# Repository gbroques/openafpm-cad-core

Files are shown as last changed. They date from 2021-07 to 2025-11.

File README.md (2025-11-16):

# OpenAFPM CAD Core

Repository containing [OpenAFPM](https://www.openafpm.net/) wind turbine CAD model, and models for tools aiding in the local construction of the wind turbine such as molds and jigs.

The wind turbine design is based on ["*A Wind Turbine Recipe Book*" by Hugh Piggott](http://scoraigwind.co.uk/pdf-metric-edition-of-recipe-book-at-scribd/).

All models are made with the open-source CAD program [FreeCAD](https://www.freecad.org/).

Various functions (yet to be described) are exposed to support other projects. See [Related Repositories](#related-repositories).

## Installing Package

From the root of this repository:

    pip install --editable .

## Installing Macros

From the root of this repository:

    ./link_macros.bash

## Related Repositories
* [openafpm_worker/MagnAFPM](https://gitlab.com/rurerg/openafpm/openafpm_worker/-/tree/master/MagnAFPM) - simulates AFPM generator and generates output for CAD model.
* [openafpm-cad-visualization](https://github.com/gbroques/openafpm-cad-visualization) - visualizes CAD models in a web browser.
* [openafpm-cad-desktop-app](https://github.com/gbroques/openafpm-cad-desktop-app) - for **testing** `openafpm-cad-core` and `openafpm-cad-visualization`.

## Prerequisites

1. Install [Micromamba](https://mamba.readthedocs.io/en/latest/installation/micromamba-installation.html).

## Setup
Execute the following commands from the root of this repository.

1. Create `openafpm-cad-core` conda environment.

       micromamba env create --file environment.yml

2. Activate `openafpm-cad-core` environment.

       micromamba activate openafpm-cad-core

3. Add the `$CONDA_PREFIX/lib` directory to `$PYTHONPATH` (this allows `FreeCAD` to be imported as a module within python).

       ./add_conda_path_to_python_path.sh

4. Deactivate and re-activate `openafpm-cad-core` environment.

       micromamba deactivate && micromamba activate openafpm-cad-core

5. Verify `freecad` executable is accessible:

       freecad --version

## Docs
Run `./make_docs.sh` from `docs/` with `openafpm-cad-core` conda environment activated.

## How to Upgrade FreeCAD Version
The version of FreeCAD is defined in `environment.yml` within the root of this repository.

1. Check if there's a newer version from FreeCAD's [GitHub releases page](https://github.com/FreeCAD/FreeCAD/releases) or [Wiki](https://wiki.freecad.org/Feature_list#Release_notes).
2. Increase version for `freecad` in `environment.yml`.
3. Remove `openafpm-cad-core` conda environment created in the "Setup" section.

       micromamba remove --name openafpm-cad-core --all

4. Reperform steps in the [Setup](#setup) section to recreate `openafpm-cad-core` conda environment.
5. Regression test all functionality. (TODO: Write documentation for this)
6. Update "Supported FreeCAD Versions" section in [README.md](./README.md).

## Generating Files for openafpm-cad-visualization

1. Activate the `openafpm-cad-core` conda environment.
2. If `openafpm-cad-visualization` is cloned up a directory from this repository, then run:

       python macros/visualize.py ../openafpm-cad-visualization/public/
       python macros/furl_transform.py > ../openafpm-cad-visualization/public/furlTransform.json

## Troubleshooting

Run `/macros` from FreeCAD's GUI to see FreeCAD related warnings and errors.

Currently, macros must be manually edited to remove multi-threading to avoid a pickle-related serialization error.

## Supported FreeCAD Versions

Currently tested with FreeCAD `1.0.0`.

## Links
* [[YouTube] Wind Empowerment Webinar - OpenAFPM tools for designing AFPM generators for Small Wind Turbines](https://www.youtube.com/watch?v=hk0j-qxkG9s&ab_channel=WindEmpowerment)
* [Wind Empowerment](https://windempowerment.com/)
* [WISIONS of Sustainability](https://wisions.net/)
* [Hugh Piggott's blog](http://scoraigwind.co.uk/)
* [[Wikipedia] Wind turbine design](https://en.wikipedia.org/wiki/Wind_turbine_design)

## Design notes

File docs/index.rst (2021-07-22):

OpenAFPM CAD Core Documentation
===============================

.. toctree::
   :maxdepth: 1
   :caption: openafpm_cad_core

   openafpm_cad_core/openafpm_cad_core

Indices and tables
==================

* :ref:`genindex`
* :ref:`modindex`
* :ref:`search`

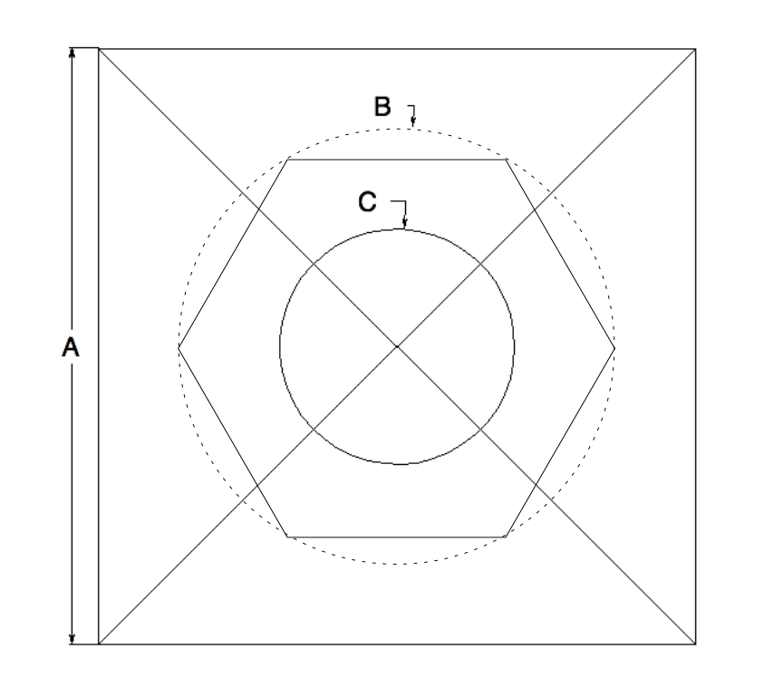
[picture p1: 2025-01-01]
openafpm_cad_core/img/star-shape-stator-mould-dimensions.png

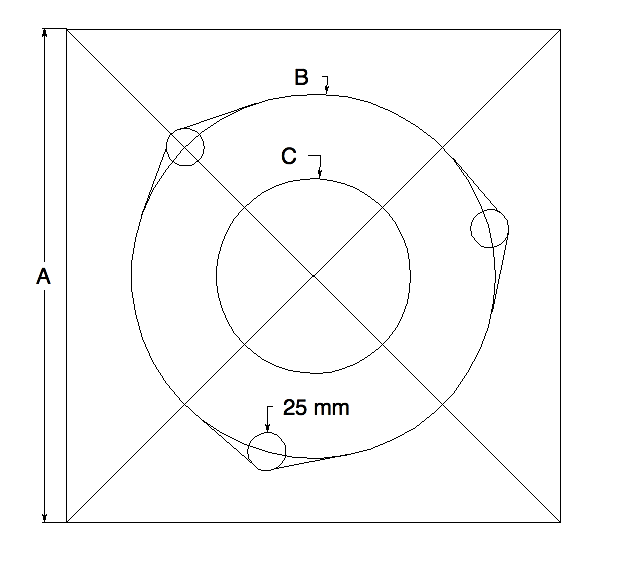
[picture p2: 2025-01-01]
openafpm_cad_core/img/t-shape-stator-mould-dimensions.png

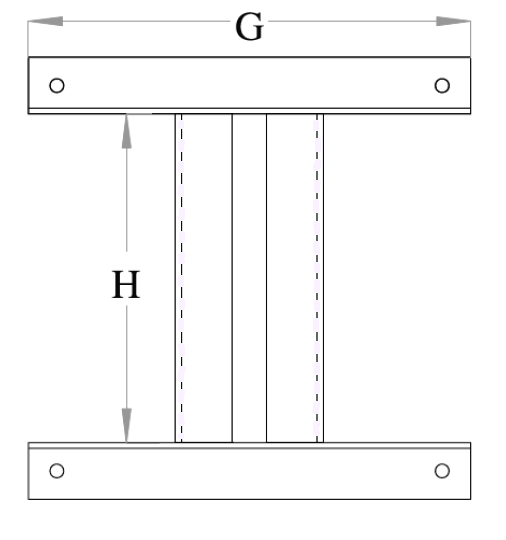
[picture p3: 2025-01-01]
openafpm_cad_core/img/h-shape-frame.png

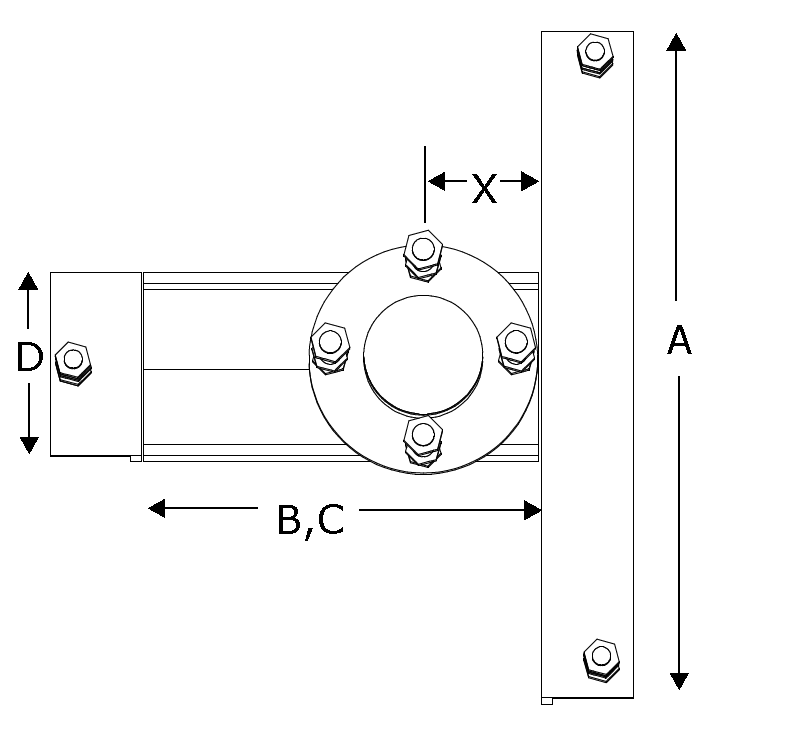
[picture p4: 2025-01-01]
openafpm_cad_core/img/t-shape-frame.png

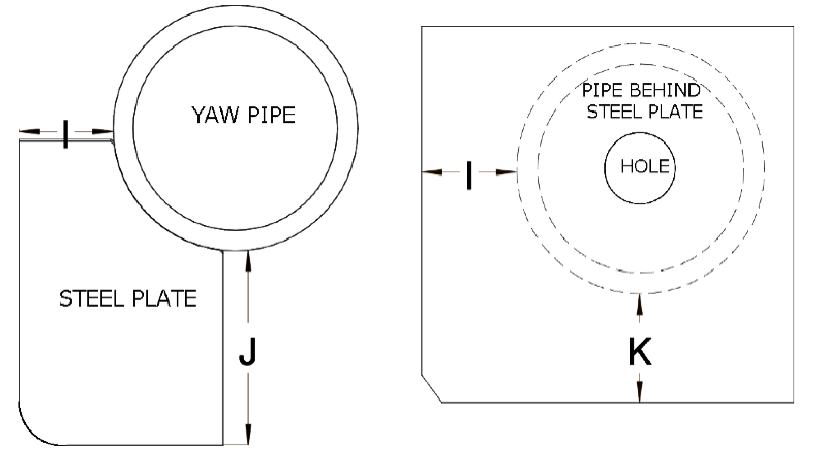
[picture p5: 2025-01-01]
openafpm_cad_core/img/t-shape-yaw-bearing-frame-junction.png

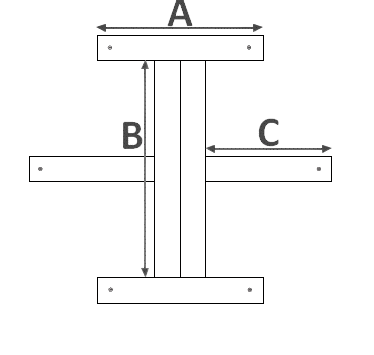
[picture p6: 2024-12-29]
openafpm_cad_core/img/star-shape-frame.png

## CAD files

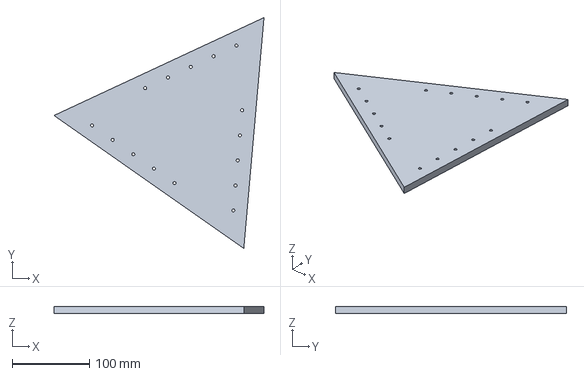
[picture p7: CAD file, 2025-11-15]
openafpm_cad_core/documents/Blades/Blade_Assembly_FrontTriangle.FCStd
271.9 x 298.9 x 9.00 mm

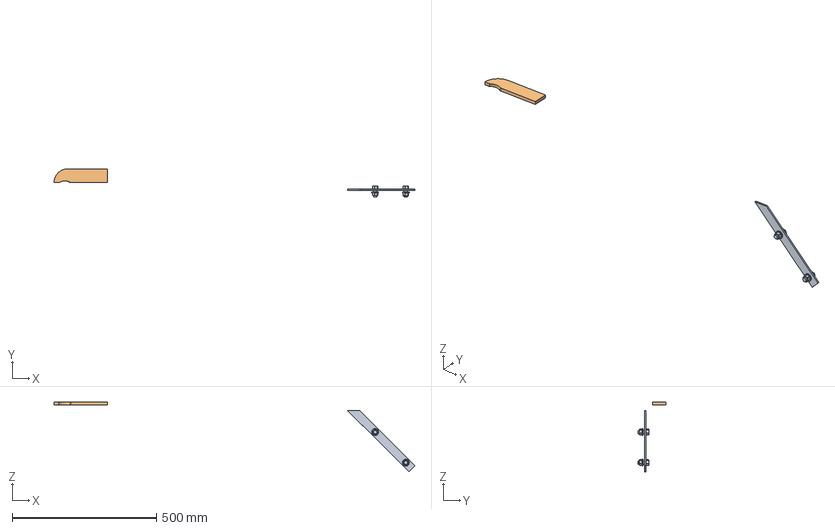
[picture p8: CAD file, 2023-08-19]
openafpm_cad_core/documents/Tail/Tail_Assembly_BoomVane.FCStd
1251.5 x 98.6 x 241.2 mm
Vane_Bracket_Bottom
Tail_Stop_HighEnd

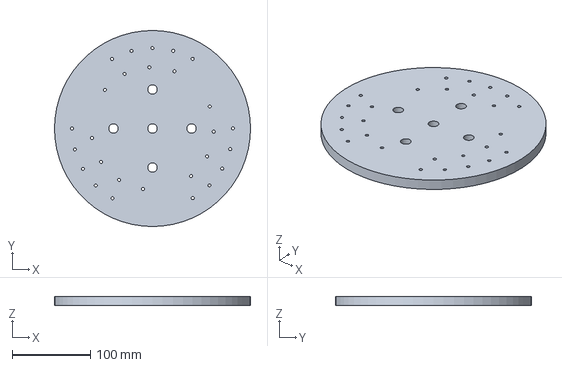
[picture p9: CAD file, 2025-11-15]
openafpm_cad_core/documents/Blades/Blade_Assembly_BackDisk.FCStd
251.0 x 251.0 x 12.0 mm

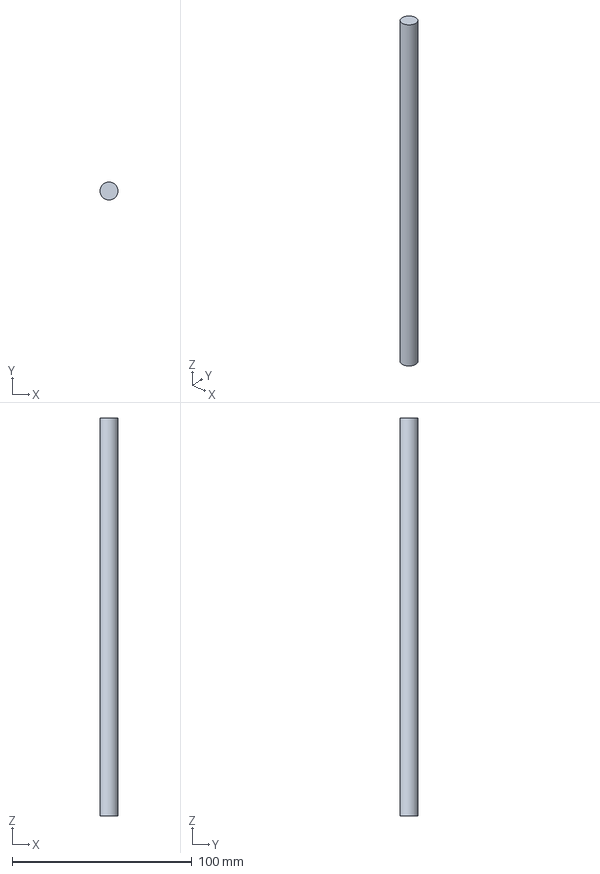
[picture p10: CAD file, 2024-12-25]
openafpm_cad_core/documents/Alternator/Stator/CoilWinder/Stator_CoilWinder_Assembly.FCStd
9.99 x 10.00 x 221.5 mm

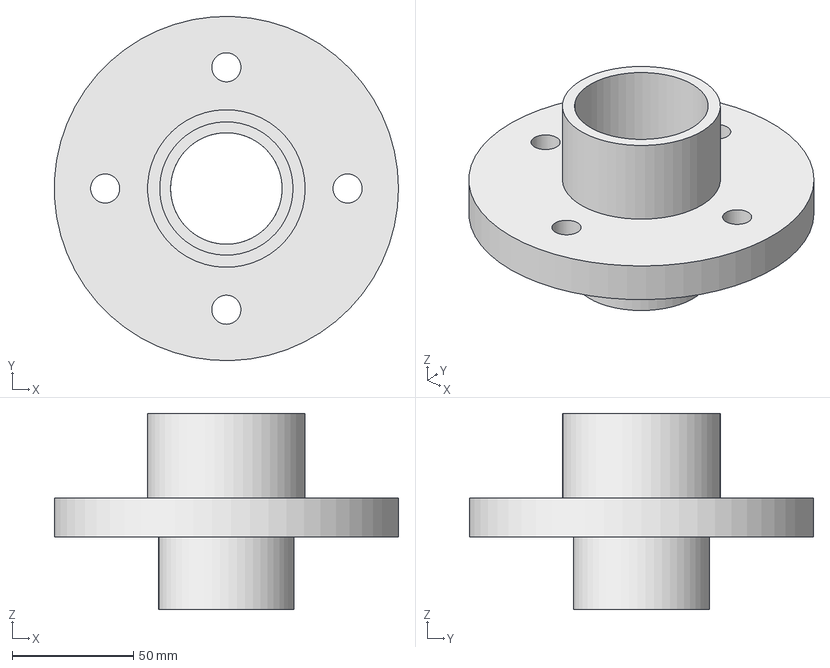
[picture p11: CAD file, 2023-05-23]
openafpm_cad_core/documents/Alternator/Hub/Hub_Flange.FCStd
141.9 x 141.9 x 81.0 mm

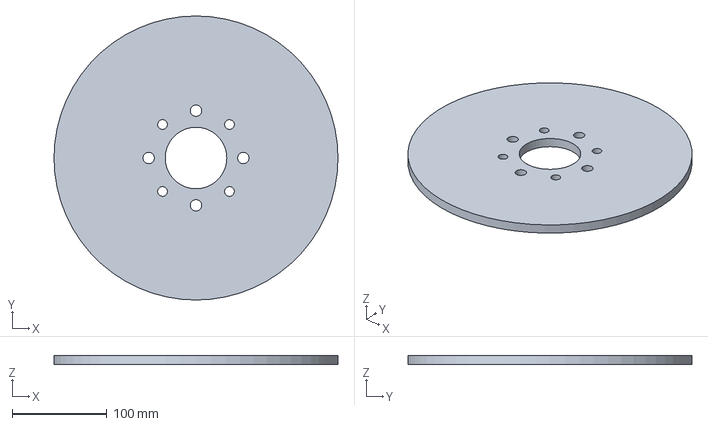
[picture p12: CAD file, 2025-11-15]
openafpm_cad_core/documents/Alternator/Rotor/Rotor_Disk_Front.FCStd
300.0 x 300.0 x 10.0 mm

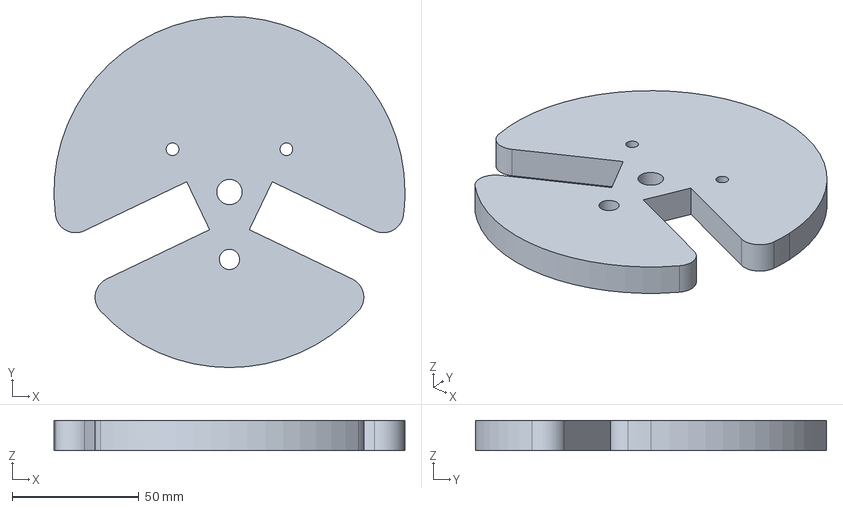
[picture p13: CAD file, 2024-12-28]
openafpm_cad_core/documents/Alternator/Stator/CoilWinder/Stator_CoilWinder_Cheek_Triangular.FCStd
138.7 x 138.7 x 12.0 mm

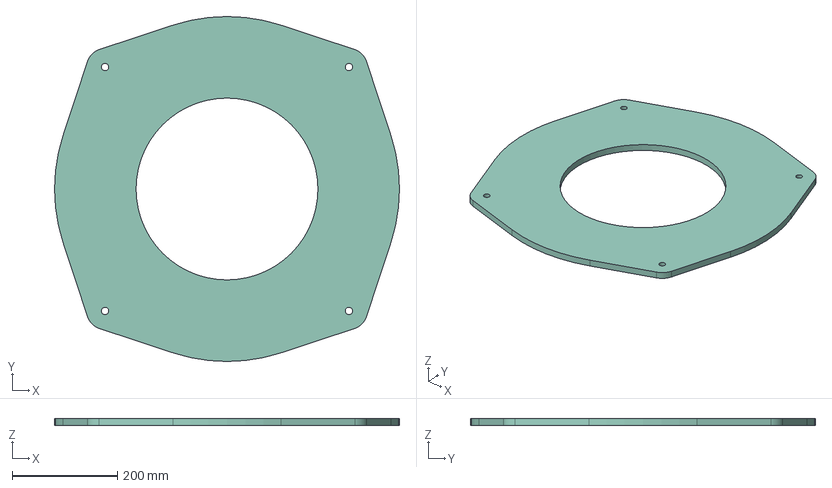
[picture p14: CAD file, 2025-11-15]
openafpm_cad_core/documents/Alternator/Stator/Stator_ResinCast_Circular.FCStd
655.4 x 655.4 x 14.0 mm

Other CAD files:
openafpm_cad_core/documents/Alternator/Rotor/MagnetJig/Rotor_MagnetJig_Assembly.FCStd
openafpm_cad_core/documents/Alternator/Rotor/Mold/Rotor_Mold_Assembly.FCStd
openafpm_cad_core/documents/Alternator/Stator/Mold/Stator_Mold_Assembly.FCStd
openafpm_cad_core/documents/YawBearing/Extended/YawBearing_Extended_Assembly.FCStd
openafpm_cad_core/documents/YawBearing/YawBearing_Assembly.FCStd
openafpm_cad_core/documents/Tail/Tail_Assembly.FCStd
openafpm_cad_core/documents/Alternator/Rotor/MagnetResin_Assembly.FCStd
openafpm_cad_core/documents/Alternator/Alternator.FCStd
openafpm_cad_core/documents/Alternator/Frame/Frame.FCStd
openafpm_cad_core/documents/Alternator/Studs/Studs_Frame.FCStd
openafpm_cad_core/documents/Alternator/Frame/Frame_Bracket_End_OneHole.FCStd
openafpm_cad_core/documents/Alternator/Frame/Frame_Bracket_End_TwoHole.FCStd
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

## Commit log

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2021-01-10 Replace rotor resin cast name and disc1 name with label
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2021-01-23 Fix using 'holes' parameter for rotor holes
    [Disc1.FCStd, Flange.FCStd]
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2021-01-31 Fix rotor webgl render; Draft.clone doesn't work in command line
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2021-02-07 Rework frame assembly to be simpler
    [EndBracket.FCStd, TailHingeEndBracketFix.FCStd]
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2021-02-27 Replace StubAxleShaft with 'Fix' version
    [StubAxleShaft.FCStd, StubAxleShaftFix.FCStd]
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2021-03-01 Fix hub dimensions; fix h shape stator
    [Flange.FCStd, FrameSideFlangeCover.FCStd, RotorSideFlangeCover.FCStd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]
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2021-03-16 Fix creating magnets and coils in wrong document
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2021-03-16 Fix issue with H Shape stator resin cast
    [StatorResinCast.FCStd]
2021-03-16 Fix t shape documents
    Add initial rotor disk parameters
    add comments to test.py
    [Disc1.FCStd, StatorResinCast.FCStd]
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2021-03-21 Merge into master of puppets doc
    Remove MasterBigWindTurbine refs in stator resin cast
    [StatorResinCast.FCStd]
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2021-04-09 Fix partial document loading issue
    [Alternator.FCStd, Coil.FCStd, CoilAssembly.FCStd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]
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2021-04-13 Fix star shape spreadsheet generation in Master of Puppets
    Update Channel to reference TShape in Master of Puppets
    [Channel.FCStd, ChannelSection.FCStd, HShapeChannelSection.FCStd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]
2021-04-14 Fix Channel positioning
    [Channel.FCStd, ChannelSection.FCStd, HShapeChannelSection.FCStd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]
2021-04-14 Fix reference to channel section height in t shape frame
    [Channel.FCStd, ChannelSection.FCStd, HShapeChannelSection.FCStd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]
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2021-04-24 Rework load turbine
    [Master of Puppets.FCStd]
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2021-05-17 Add LargeWindTurbine for H Shape and Star Shape yaw bearing - alternator assembly
    [LargeWindTurbine.FCStd, WindTurbine.FCStd]
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2021-05-18 Add formulas for Yaw Bearing X, Y, and Z for large wind turbine
    [LargeWindTurbine.FCStd]
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2021-05-22 Make Top sketch fully constrained
    Use formula based on Offset for Length
    Get rid of triangular corner
    [Top.FCStd]
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2021-05-24 Replace with Star Shape
    [Master of Puppets.FCStd]
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2021-05-24 Replace Pocket with Hole
    [RightMiddleBracket.FCStd]
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2021-06-01 Rework top cover to be less angular
    Make cheek pieces lay at a slight angle
    [TShapeWindTurbine.FCStd, TailHinge.FCStd, TailHingeTopCover.FCStd]
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2021-06-06 Fix TailHinge Y for Star Shape
    [LargeWindTurbine.FCStd]
2021-06-06 Clean up; fix last fix works for H + Star Shape
    [LargeWindTurbine.FCStd]
2021-06-06 Fix X axis alignment issue with rear side cover
    [TailHinge.FCStd]
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2021-06-06 Fix more alignment issues and calculations
    [TailHinge.FCStd]
2021-06-06 Add missing parameter bindings
    [TailHinge.FCStd]
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2021-06-11 Update Master of Puppets#Spreadsheet with new calculations for tail hinge junction width
    [Master of Puppets.FCStd]
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2021-06-15 Fix TailVane and Bracket holes alignment issue
    [Tail.FCStd, TailBoom.FCStd, TailVane.FCStd]
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2021-06-17 Switch TailHinge link to TailHingeAssembly in TShapeWindTurbine
    Need to re-orient a few parts
    Also account for 55 degree angle
    [Flange.FCStd, Frame.FCStd, OuterTailHinge.FCStd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]
2021-06-20 Invert tail boom pieces for proper orientation
    [OuterTailHinge.FCStd, OuterTailHingeHighEndStop.FCStd, TShapeWindTurbine.FCStd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]
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2021-07-08 Finish calculations for TailBoom placement at 100 deg angle for T Shape
    [TShapeWindTurbine.FCStd, TailBoom.FCStd, TailBoomTriangularBrace.FCStd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]
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2021-07-08 Rework TailHingeAssembly for viz export
    [LargeWindTurbine.FCStd, TShapeWindTurbine.FCStd, TailHinge.FCStd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]
2021-07-08 Possibly fix Top sketch alignment issue
    [Top.FCStd]
2021-07-09 Rework documents so that vane is separate
    [Tail.FCStd, TailBoom.FCStd, TailHingeAssembly.FCStd]
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2021-07-09 Invert T Shape Frame
    Still need to invert 'bottom plate'
    [Alternator.FCStd, TShapeChannelSection.FCStd]
2021-07-09 Reorient bottom plate into correct place
    [TShapeFrame.FCStd]
2021-07-09 Fix Frame Y position for T Shape
    [Alternator.FCStd, Frame.FCStd]
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2021-07-09 Fix orientation of TailHingeAssembly
    [LargeWindTurbine.FCStd]
2021-07-09 Attempt to fix RightMiddleBracket Sketch
    [Master of Puppets.FCStd, RightMiddleBracket.FCStd]
2021-07-09 Attempt to fix RightMiddleBracket Sketch again
    Fix alignment of coils in SixHoleStatorResinCast
    [LeftMiddleBracket.FCStd, RightMiddleBracket.FCStd, SixHoleStatorResinCast.FCStd]
2021-07-09 Fix Coils alignment for Four hole stator resin cast
    Update four hole stator resin cast to conventions
    [FourHoleStatorResinCast.FCStd, Master of Puppets.FCStd]
2021-07-09 Fix Vane bracket holes alignment for H Shape
    [Master of Puppets.FCStd, Tail.FCStd, TailVane.FCStd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]
2021-07-09 Update default star shape paarams
    Rework coil document a bit
    [Coil.FCStd]
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2021-07-09 Reverse orientation of Vane and Stop
    [Tail.FCStd]
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2021-07-10 Fix T Shape Frame alignment issue
    Fix T Shape Yaw Bearing positioning in SmallWindTurbine
    [Alternator.FCStd, Master of Puppets.FCStd, OneHoleEndBracket.FCStd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]
2021-07-10 Fix TailVane Sketch Issue
    [Tail.FCStd, TailVane.FCStd]
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2021-07-10 Add colors to FreeCAD model
    Green epoxy resin, wood, copper coils, and magnet colors
    [Coil.FCStd, FourHoleStatorResinCast.FCStd, Magnet.FCStd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]
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2021-07-10 Fix hole alignment issue for H Shape
    [TwoHoleEndBracket.FCStd]
2021-07-10 Make angle negative to fix alignment
    [OuterTailHinge.FCStd]
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2021-07-12 Continue adjusting low end stop for tighter fit
    [OuterTailHingeLowEndStop.FCStd]
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2021-07-14 Fix Rotor Disk small holes alignment for Star Shape
    [Master of Puppets.FCStd, RotorDiskReducedWeight.FCStd]
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2021-07-16 Delete BottomTailVaneBracket link from Tail
    Set apperance to Chrome for Bolt / HexNut
    [Bolt.FCStd, HexNut.FCStd, Tail.FCStd]
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2021-07-21 Make spacing between holes for tail vane bracket more spaced out
    For H & Star Shape
    [TailVane.FCStd]
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2021-08-22 Correct Large Alternator orientation
    [Master of Puppets.FCStd, WindTurbine.FCStd]
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2021-08-28 Move boom 1cm from top of tail hinge
    Make triangular support flush with bottom of tail hinge
    [Master of Puppets.FCStd, TailBoomTriangularBrace.FCStd, TailHingeAssembly.FCStd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]
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2021-08-30 [WIP] Shorten side of extended yaw bearing
    [ExtendedYawBearingPipe.FCStd, Side.FCStd, Top.FCStd]
2021-08-30 Shorten side of extended yaw bearing
    [ExtendedYawBearingPipe.FCStd, Master of Puppets.FCStd, Side.FCStd]
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2021-08-31 Make YawBearingTailHingeJunctionHeight dynamic instead of static
    Yaw bearing tail hinge junction is now proportional
    [Master of Puppets.FCStd]
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2021-09-01 Attempt to fix Tail Vane sketch
    [TailVane.FCStd]
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2021-09-18 Fix orientation of ArcWireSupport for T Shape
    [ArcWireSupport.FCStd, Master of Puppets.FCStd, TShapeYawBearingPipe.FCStd]
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2021-09-20 Attempt to fix hex nut issue
    [HexNut.FCStd]
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2021-09-20 Fix hub thread length reference
    [Alternator.FCStd]
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2021-09-20 Make stator mounting studs short
    [Master of Puppets.FCStd, StatorMountingStud.FCStd, StatorMountingStudArray.FCStd]
2021-09-21 Fix Y position of BackTailHingeSideCover
    [YawBearingTailHingeJunction.FCStd]
2021-09-22 Add nuts and washers on rotor mounting stubs
    Also called hub threads
    To keep disks separated
    [HubHexNut.FCStd, HubThread.FCStd, HubWasher.FCStd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]
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2021-09-29 Shorten SideLength to not file down edge
    The gap can be welded
2021-10-03 Ensure Offset is correct for H Shape
    [Master of Puppets.FCStd, Side.FCStd, Top.FCStd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]
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2021-10-03 Fix t shape offset
    [Master of Puppets.FCStd, TwoHoleEndBracket.FCStd]
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2021-10-03 Fix spacing between Frame & Hub for Star Shape
    [Master of Puppets.FCStd, StatorMountingStud.FCStd]
2021-10-28 Reference HighEndStop spreadsheet for width & length
    Clean up rotation logic with vector math in spreadsheet
    [Master of Puppets.FCStd, OuterTailHingeHighEndStop.FCStd]
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2021-10-28 Attempt to fix Alternator axis issue
    [Alternator.FCStd]
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2021-10-28 Fix positioning of safety catch
    [TShapeYawBearingPipe.FCStd]
2021-10-30 Support furling tail
    Rework HighEndStop sheet to use translated YawBearing center
    Bind placements defined in HighEndStop sheet
    Expose furl transforms
    Fix furl_tail.py macro
    [ExtendedYawBearingPipe.FCStd, Master of Puppets.FCStd, Tail.FCStd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]
2021-11-03 Limit filesystem modification to spreadsheet document
    Rename <<Master of Puppets>> label refs to Master_of_Puppets
    Add better type hints for get_furl_transforms
    Rework macros for parallel execution of T, H, & Star
    Ignore Master_of_Puppets.FCStd in source control
    Refactor archive export
    [Alternator.FCStd, ArcWireSupport.FCStd, Bolt.FCStd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]
2021-11-03 Make magnets slightly thinner than resin cast
    To fix z-fighting issue & keep mechanical clearance accurate
    [Magnet.FCStd, RotorResinCast.FCStd]
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2021-11-07 Correct links to Washers
    [StatorMountingStudArray.FCStd]
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2021-11-10 Replace TailBoom with TopTailVaneBracke in keep_unresolved
    For proper .obj export
    [TailBoomVaneAssembly.FCStd]
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2021-11-12 Fix coil overlap issue by reducing leg width for T Shape
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2021-11-13 Adjust Z position of High End Stop
    To center stop with yaw bearing contact point for Star Shape
    [Tail_Assembly_BoomVane.FCStd]
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2021-11-25 Fix RotorSide column grouping for Hub sheet
    Clean up duplicated definitions of Hub parameters
    [Hub_Flange_Cover_Back.FCStd, Hub_Flange_Cover_Front.FCStd]
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2021-11-25 Fix YawBearingY position bug
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2021-11-29 Fix Yaw and Roll rotation order for Alternator
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2021-12-19 Fix spacing between Frame & Hub for Star Shape
    HShape: MetalLengthL 50 -> 60
    StarShape: MetalLength 65 -> 80
    [Hub.FCStd, Hub_StubAxleShaft.FCStd, Studs_Frame_Base.FCStd]
2021-12-26 Make HighEndStop straight
    Decrease Y padding for safety catch by 3 mm
    [Tail_Stop_HighEnd.FCStd]
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2022-02-06 Fix rotor resin cast inner radius for H Shape
    [Rotor_ResinCast.FCStd]
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2022-02-20 Add jacking holes to front rotor disk for T & H Shape
    [Alternator.FCStd, MagnetResin_Assembly.FCStd, Rotor_Back.FCStd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]
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2022-03-19 Fix stator mold
    [Stator_Mold_BoltShaftLayer_Circular.FCStd, Stator_Mold_Surround_Circular.FCStd]
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2022-04-05 Use same dist from circ edge for rotor mold screws for all 3 shapes
    [Rotor_Mold_Base.FCStd]
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2022-04-10 Fix lid notch sketch
    [Stator_Mold_Lid.FCStd]
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2022-04-23 Add 5mm space to rotor mold lid holes
    For resin to flow out
    Also add more bolt sizes to lookup table
    [Rotor_Mold_Lid.FCStd]
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2022-04-24 Update triangular coil winder
    Make outer edge of pin holes equidistant from center
    [Stator_CoilWinder_Assembly.FCStd, Stator_CoilWinder_Cheek.FCStd, Stator_CoilWinder_Cheek_Notch.FCStd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]
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2022-04-28 Fix notch pocke
    [Stator_CoilWinder_Cheek_Notch.FCStd, Stator_CoilWinder_Cheek_Triangular.FCStd]
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2022-07-04 Update conduit for wires macro with transaction
    and fix resolving symlink to rotor resin cast
    [Stator_Mold_Assembly.FCStd, Stator_Mold_Lid.FCStd]
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2022-10-02 Add ability to load ALL assemblies at once
    For debugging issues with load_all function
2022-10-02 Fix export to dxf
    [Stator_Coil.FCStd, Stator_CoilWinder_Assembly.FCStd, Stator_CoilWinder_Cheek.FCStd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]
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2022-10-10 Fix outer magnet jig link
    Create threshold var for inner dist. between magnets
    [Rotor_MagnetJig_Assembly.FCStd]
2022-10-10 Separate bolts and nuts into 2 arrays
    For visualization and OBJ export
    [Rotor_MagnetJig_Assembly.FCStd]
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2022-10-22 Enable BindCopyOnChange; fix parameterization
    [Fastener_HexNut_HubHoles.FCStd]
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2022-10-23 Fix hex nut missing StatorMold variant
    [Fastener_HexNut.FCStd, Fastener_HexNut_StatorMold.FCStd, Stator_Mold_BoltHeadLayer_Circular.FCStd]
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2022-11-01 Add line from middle right to top right to Alternator spreadsheet
    For hexagonal mold
    Reference newly added parameters
    [Stator_Mold_BoltHeadLayer_Hexagonal.FCStd, Stator_Mold_BoltShaftLayer_Circular.FCStd, Stator_Mold_BoltShaftLayer_Hexagonal.FCStd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]
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2022-11-14 Fix CoilInnerWidth1 constraint for triangular
    [Stator_Coil.FCStd]
2022-11-14 Fix triangular coil
    [Stator_Coil.FCStd, Stator_CoilWinder_Assembly.FCStd, Stator_Coil_Triangular.FCStd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]
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2022-11-20 Hide washer, nuts, and bolts from inverted magnet jig
    [Rotor_MagnetJig_Assembly.FCStd]
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2022-12-11 Add wood screw and fix surround screws length
    [Fastener_WoodScrew_M5x25.FCStd, Stator_Mold_Assembly.FCStd, Stator_Mold_BoltHeadLayer_Hexagonal.FCStd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]
2022-12-11 Fix rotor mold screw length
    [Fastener_WoodScrew_M5x25.FCStd, Fastener_WoodScrew_M5x30.FCStd, Fastener_WoodScrew_RotorMold.FCStd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]
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2022-12-11 Fix tip threads not exporting for stator mold screws
    [Fastener_WoodScrew_M5x25.FCStd, Fastener_WoodScrew_RotorMold.FCStd, Stator_Mold_BoltShaftLayer_Circular.FCStd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]
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2023-01-28 Fix Fastener_WoodScrew_RotorMold link issue
    [Fastener_WoodScrew_RotorMold.FCStd]
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2023-02-07 Align magnets to disk based on corners
    As opposed to midpoint of magnet aligning to edge of disk
    [Rotor_MagnetJig_Disk.FCStd, Rotor_MagnetJig_Outer.FCStd, Rotor_Magnets.FCStd]
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2023-02-19 Fix coil winder visualization export
    [Stator_CoilWinder_Assembly.FCStd]
2023-02-21 Align stator mounting points with middle space between 2 coils instead of the middle of 1 coil
    [Stator.FCStd, Stator_Coils.FCStd]
2023-02-27 Revert "Align stator mounting points with middle space between 2 coils instead of the middle of 1 coil"
    This reverts commit 3b51a669ded46064eb21406c27bc21d7bda9e017.
    [Stator.FCStd, Stator_Coils.FCStd]
2023-03-05 Fix BottomPlateX formula
    Use FlatMetalThickness instead of MetalThicknessL
    [Frame_Shape_T.FCStd]
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2023-04-29 Fix coils extending a couple mm beyond inner resin
    [Stator_ResinCast_Circular.FCStd]
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2023-05-07 Add steel angle section width / thickness to 'Frame Dimensions' table
    Fix casing of Central hole diameter
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2023-05-28 Fix yaw pipe diameter enum
2023-05-31 Fix chamfer for top plate of t shape
    [YawBearing_ArcWireSupport.FCStd, YawBearing_Assembly.FCStd, YawBearing_Extended_Assembly.FCStd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]
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2023-07-15 Fix HubZ calculation causing hub & stubs to appear moved back to frame
    This bug was introduced in commit 868af5a174f14e12fa44554dfe60997ae971e0ed
    [Alternator.FCStd]
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2023-07-22 Fix gap between side piece and yaw bearing pipe for H & Star shape
    This occurred when increasing the default MetalLengthL by 10mm (e.g. from 60 to 70 mm for H Shape)
    There's still a gap between the side piece and yaw bearing pipe, but that could be fixed by increasing FlatMetalThickness
2023-07-22 Use LargestMagnetDimension instead of MagnetLength for TriangularCoilHoleHeight
    To avoid model breaking when MagnetWidth is greater than MagnetLength (e.g. 50 & 30 respectively)
2023-07-22 Fix SafetyCatch not binded to placement parameters
    [YawBearing_Extended_Assembly.FCStd]
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2023-07-24 Prevent switching to Tail document automatically for furl_tail macro
2023-08-06 Rework low end stop to support 20° VerticalPlaneAngle for H & Star
    Move 'Tail Hinge Pipe X Z' section above 'OuterPipe' subsection for
    HingeOuterPipeLength formula to use h1 & h2.
    Perform cut for low end stop & yaw bearing cylinder.
    MaximumFurlAngle calculation is relative to Tail_Assembly document instead of global.
    Fallback to label if cell doesn't have alias in create_point macro
    [Tail_Assembly.FCStd, Tail_Hinge_Outer.FCStd, Tail_Stop_LowEnd.FCStd]
2023-08-06 Fix Groove for HexNut
    [Fastener_HexNut.FCStd]
2023-08-06 Fix one size up yaw pipe option for T Shape
    Rework I based on X
    Rework X based on right triangle and StatorHolesCircumradius
    [Frame_Bracket_End_TwoHole.FCStd]
2023-08-06 Always center hole when viewing brackets from front of turbine for T Shape
    [Frame_Bracket_End_TwoHole.FCStd]
2023-08-07 Clean up hole margin for frame
    Should always be MetalLengthL / 2 consistently for each shape
    Fixup T Shape yaw bearing placement which shouldn't depend on hole margin
    [Frame_Bracket_End_TwoHole.FCStd, Frame_Bracket_Middle.FCStd, Frame_Shape_T.FCStd]
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2023-08-14 Rework high end stop for safety catch
    Make safety catch perpendicular to boom
    Make safety catch stretch to about half-way to boom
    Remove HighEndStop sheet dependency on WindTurbine sheet
    Simplify the how the high end stop was done, and improve the algorithm
    [Tail_Assembly_BoomVane.FCStd, Tail_Stop_HighEnd.FCStd, Tail_Stop_LowEnd.FCStd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]
2023-08-19 Fix coil winder when magnet width is larger than length
    Occurs for Star shape when
    MagnetLength = 30
    MagnetWidth = 50
    CoilInnerWidth1 = 70
    CoilInnerWidth2 = 30
    [Stator_Coil.FCStd, Stator_CoilWinder_Cheek.FCStd, Stator_CoilWinder_Spacer.FCStd]
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2023-08-20 Fix DXF export for low end stop
    [Tail_Hinge_Outer.FCStd, Tail_Stop_LowEnd.FCStd]
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2023-08-25 Fix 'section' typo
    [Frame_Shape_Star.FCStd]
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2023-09-07 Fix safety catch 'moving back' for Star Shape
    When vertical plane angle is 20° and horizontal plane angle is 70°
    [YawBearing_Assembly.FCStd, YawBearing_SafetyCatch.FCStd]
2023-09-09 Fix gap between boom and hinge
    Bug was introduced in commit e1c727e
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2023-09-11 Align triangular notch on coil winder disk with bottom of coil for T Shape 2F
    [Stator_CoilWinder_Cheek_Notch.FCStd]
2023-09-14 Reset HingeOuterPipeDiameter to YawPipeDiameter
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2023-11-04 Always extend low end stop right before boom support starts
    Fixes low end stop & boom support overlap issue for H Shape 20° VerticalPlaneAngle
    [Tail_Stop_LowEnd.FCStd]
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2023-11-27 Increase CoilY for Triangular coils
    Fix island-coil overlap issue
    [Stator_Coils.FCStd]
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2023-12-26 Decrease CoilY for Triangular coils
    Effectively reverts commit:
    5153d067d50e8327a2e9ee5c9c70657a1101d0bf
    BEFORE
    =CoilType != 3 ? DistanceOfMagnetFromCenter - CoilLegWidth : DistanceOfMagnetFromCenter + CoilLegWidth
    AFTER
    =CoilType != 3 ? DistanceOfMagnetFromCenter - CoilLegWidth : DistanceOfMagnetFromCenter
    There is not island-coil overlap issue with T Shape 2F
    and H Shape 4F variants.
    [Stator_Coils.FCStd]
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2023-12-28 [H & Star] Fix small gap between yaw pipe & side piece
    Accomplished by moving side piece in towards pipe if there's room
    Testing notes: Set MetalLengthL to 70 for H Shape default values
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2024-03-04 Fix coil winder for other parameters besides H Shape 4F
    [Stator_CoilWinder_Assembly.FCStd, Stator_CoilWinder_Cheek_Notch.FCStd, Stator_CoilWinder_Cheek_Triangular.FCStd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]
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2024-03-10 Fix reference to YawBearing.YawPipeLength to HighEndStop.YawPipeLength
2024-03-11 Fix alignment of triangular coils with magnets
    Needed to move Y positino adjustment from Coil to Coils array for freecad-to-obj to properly export these
    [Stator_Coil_Triangular.FCStd, Stator_Coil_Triangular_Reduced.FCStd, Stator_Coils.FCStd]
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2024-03-30 Fix user and furling parameters positions for assembly_to_obj function
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2024-04-04 Add Master_of_Puppets.FCStd to git
    Fixes a segfault with create_archive
    git can ignore changes to the file by running:
    git update-index --assume-unchanged openafpm_cad_core/documents/Master_of_Puppets.FCStd
    [Master_of_Puppets.FCStd]
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2024-04-13 Rotate front triangle to avoid blade edge crossing a hole
    [Alternator.FCStd, Blade_Assembly_BackDisk.FCStd, Blade_Assembly_FrontTriangle.FCStd]
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2024-04-13 Fix number of holes should be 5 for H Shape
    [Rotor_Disk_Back_ReducedWeight.FCStd]
2024-04-13 [MagnetJig] Use reduced weight rotor disk when RotorDiskRadius exceeds 230 mm
    Fixes regular rotor disk from showing up in DXF export
    [Rotor_MagnetJig_Assembly.FCStd]
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2024-05-03 Fix placement of outer screw line to evenly space between hub holes & edge
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2024-05-12 Fix fillet for triangular cheek piece
    [Stator_CoilWinder_Cheek_Triangular.FCStd]
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2024-05-14 Angle side piece to fix gap between it & frame
    Necessary for Star Shape when MetalLengthL is 100
    Also occurs for H Shape when MetalLengthL is 70
    [YawBearing_Extended_Assembly.FCStd]
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2024-05-17 Fix ArcWireSupportX calculation
    Fixes arc wire support alignment for small wind turbine
    [YawBearing_Assembly.FCStd]
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2024-05-19 Fix root of blade template
    By using 120° constraint instead of 2W length constraint
    [Blade_Template.FCStd]
2024-05-19 Fix alignment and rotation of middle bolt
    [Stator_Mold_BoltHeadLayer_Circular.FCStd, Stator_Mold_BoltShaftPattern_Circular.FCStd]
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2024-05-21 Fix triangular spacer breaking on small hoverboard design
    [Stator_CoilWinder_Spacer_Triangular.FCStd]
2024-05-25 Fix coil winder pin diameter reference
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2024-05-25 Fix broken M3 nuts for coil winder
    [Fastener_HexNut.FCStd]
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2024-05-31 Add list of presets for easier manual testing
    Rework main load macro / task panel for this
    Add additional parameter combinations for magnet width > length
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2024-06-05 [H & Star Shape] Prevent limiting tail support width to half outer hinge C
2024-07-05 Fix discontinuity in high end stop DXF by simplifying sketch
    [Tail_Stop_HighEnd.FCStd]
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2024-07-21 Fix tail support exceeding outer hinge in small turbines
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2024-07-25 Prevent coil from breaking in 4F 1500W 10m_s Ferrtite 150x100x25.json
    [Stator_Coil.FCStd]
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2024-07-27 Fix surround breaking in '2N MWT Hoverboard 20 pole SIM 9033_18_05_24'
    [Stator_Mold_Surround_Circular.FCStd]
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2024-08-06 Fix island screw alignment. See commit body
    for 2N MWT Hoverboard 150 RotorDiskRadius, 32 NumberMagnet case
    [Stator_Mold_BoltShaftLayer_Circular.FCStd]
2024-08-07 Fix stator mold island screw alignment for H Shape
    Remove InnerScrewsPartAngle
    [Stator_Mold_BoltShaftLayer_Circular.FCStd]
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2024-12-04 [H & Star] Add cover to inner tail hinge pipe
    Increasing the surface area of the inner tube with a cover helps prevent damage to the outer tube cover caused by friction and wear in larger turbines, especially for Star and larger H shapes.
    [Tail_Hinge_Inner_Pipe_Cover.FCStd, Tail_Hinge_Outer.FCStd]
2024-12-04 Fix coil winder visualization
    [Stator_CoilWinder_Assembly.FCStd]
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2024-12-16 Remove StatorMoldSketchAngle from LargeHoleInnerSketch
    Caused misalignment in H Shape stator moldLargeHoleInnerSketch
    [Stator_Mold_BoltShaftPattern_Circular.FCStd]
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2024-12-22 Increase StarShapeLidNotchApproximateDegrees for 20 pole case
    Also avoids overlapping bolt in 16 pole case
2024-12-22 Fix alignment of tape notch with spacer
    [Stator_CoilWinder_Cheek_Triangular.FCStd]
2024-12-25 [Blade_Assembly_FrontTriangle] Replace InnerScrewLineDistanceFromCenterOffset with Suppressed property
    Suppressed property available since FreeCAD 1.0
    [Blade_Assembly_FrontTriangle.FCStd]
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2024-12-26 Fix coil winder for small magnets
    Was breaking on '1.2N MWT Hoverboard 16 pole 24V'
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2024-12-26 Prevent Stator_Coil_Triangular_Reduced from breaking in more non-triangular scenarios
    [Stator_Coil_Triangular_Reduced.FCStd]
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2025-01-01 Rerrange single rotor topology
    Avoid overlap with stator coils & hub studs by reversing generator parts
    [Alternator.FCStd, Studs_Frame_Base.FCStd, Studs_Hub_Base.FCStd]
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2025-01-01 Fix stator mould dimensions image
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2025-01-05 Make hub studs flush with nuts on frame-side in single rotor topology
    To avoid threads from overlapping with coils
    [Alternator.FCStd, Studs_Hub_Base.FCStd]
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2025-01-21 Revert "Reduce inner tail hinge cover thickness from 5 to 3mm"
    This reverts commit 82df4be16adcc058e0535354ea7de5a683ae0587.
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2025-09-08 Fix tail vane bracket holes misalignment
    Design: 4.5N 48V Hyki 10138.json
    Email: Tail vane holes
    [Tail_Vane.FCStd]
2025-09-08 Fix tail vane holes / bolts alignment for T Shape
    [Tail_Vane.FCStd]
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2025-10-21 Fix 'Rotor disk assembly nuts' count
2025-10-21 Fix 'Rotor disk assembly washers (standard)' count
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2025-11-14 Pin Qt to 6.7.x to fix FreeCADGui import error
    Related to qt_blur symbole not found
    Symbol not found: __Z12qt_blurImageP8QPainterR6QImagedbbi
2025-11-14 Add missing type to schema for RotorTopology and WindTurbineShape
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2025-11-15 Fix 'minimum' as 'maximum' for magnet length & width schema
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
